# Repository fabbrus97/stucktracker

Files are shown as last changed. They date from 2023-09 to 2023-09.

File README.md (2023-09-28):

# StuckTracker

> [!WARNING]  
> **Experimental work**: This is experimental work. The end result does not function as intended. 

---

This repository contains all the source files - and the report - for the Making class project, at Università di Bologna. 

The aim of the project is to build a self-aligning star tracker, using 3D printed and off-the-shelf components. 

Most of the folders have a `README` with additional information. The repository is organized as follows:

- **bom**: contains the bill of material. 
- **cad**: contains the `.stl` files to be printed, and the original cad file. 
- **code**: contains the python source code, and a `systemd` service file. 
- **report**: contains the report of the project.

> [!NOTE]  
> The electronic schematics are inside the report.

---

Special thanks to Arianna, Stefano, Alessandro and Lorenzo who gave me help throughout the project.

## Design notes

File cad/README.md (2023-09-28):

# CAD Files
This folder contains the cad files.

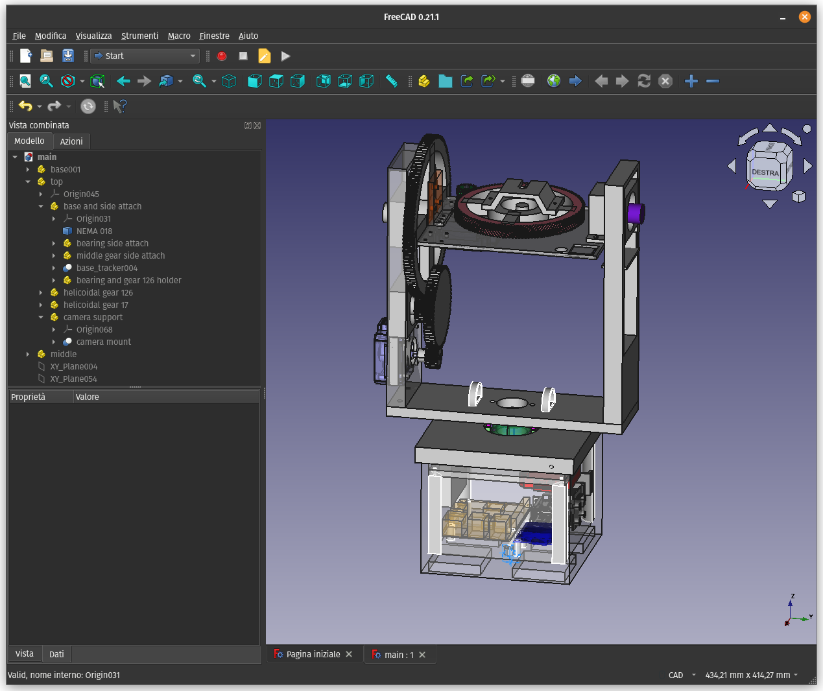
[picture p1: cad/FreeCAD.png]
FreeCAD screenshot.


The files were developed using the FreeCAD software; the main file, containing all the parts, is `main.FCStd`. 

The `std` folder contains all the `.std` files exported from FreeCAD, and organized in subfolders according to their placement and purpose.

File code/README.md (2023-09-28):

# Code
This folder contains the code to run the star tracker. The code was developed for a Raspberry Pi 3B+, and is entirely written in Python.

The required libraries can be installed as root with:
```
# pip3 install -r requirements.txt
```

Furthermore, `startracker.service` can be installed with:
```
# mv startracker.service /etc/systemd/system/
# enable startracker.service
```

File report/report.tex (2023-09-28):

\documentclass[]{article}

\usepackage{pgfplots} 
\usepackage{graphicx}
\usepackage{subfigure}
\usepackage{floatflt}
\usepackage{float}
\usepackage{hyperref}
\usepackage{mathtools}
\usepackage{tikz}
\usepackage{pgf}
\usepackage{cleveref}
\usepackage{xcolor}
\usetikzlibrary{calc,patterns,angles,quotes}
\usepackage{makecell}
\usepackage{tabularx}
\usepackage{listings}
\usepackage{svg}
\usepackage{tablefootnote}
\usepackage[most]{tcolorbox}

\newcommand{\inctrimpic}[2][1]
{}

\include{LaTeX.Listings}
\lstset{style=colorEX}

%opening
\title{Semi-Automatic Portable Star Tracker}
\author{Simone Fabbri \\ simone.fabbri8@studio.unibo.it}

\begin{document}

\maketitle

\begin{figure}[h]
	\centering
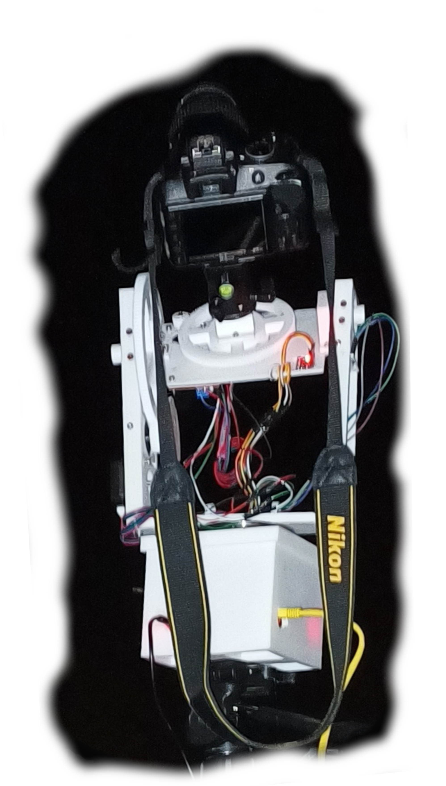
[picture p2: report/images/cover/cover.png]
	
\end{figure}

\begin{abstract}
This is the report of the project developed for the making class at the Computer Science course, university of Bologna.
\\
The scope of this project is to make a portable star tracker, with auto-alignement capability. Star trackers are very useful to photograph stars at night, since longer exposures are required. 
\\
In the following sections will be discussed the main motivations behind this project, the technical details and the conclusion of the report.

\end{abstract}

\begin{tcolorbox}[colback=red!5!white,colframe=red!75!black]
	\textbf{Warning} this is \textit{experimental} work. While the procedure is accurately documented and replicable, the end result is not working, i.e. it does not produce the expected results according to the design goals. The "Results" section shows what can be accomplished in terms of obtainable images. A list of errors and problems can be found in the "Conclusion" section. 
\end{tcolorbox}

\section{Introduction}

\begin{floatingfigure}[r]{0.30\linewidth}
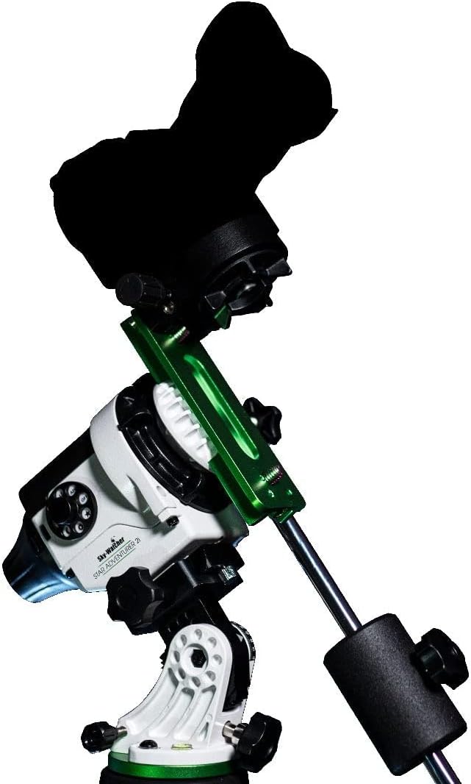
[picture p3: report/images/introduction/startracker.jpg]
	
	\caption{A commercial 500\$ star tracker, the \textit{Skywatcher Star Adventurer 2i.\\}}
\end{floatingfigure}

Capture images of stars is not a trivial task: since they don't emit a lot of light, cameras have a harder time capturing it. 

The only way to capture in a somewhat recognizable way a scarce source of light, is to use a longer time exposure: keeping the camera sensor open for longer time, allows more light to pass. 

But this can only work well for still objects: while stars technically do not move, the earth does, thus the stars seem to move during the night. If a sensor is left open for too much time, a so called "star trail" will start to appear, because the stars will have moved since the start of the capture and their traces will be left on the camera sensor.

To contrast this effect, two solution were developed in the field of photography: 

\begin{itemize}
	\item photo stacking
	\item star tracking
\end{itemize}

The first solution, \textbf{photo stacking}, consists of taking multiple shorter pictures where the stars appear still, i.e. without trails and, using specialized software, "merge" them together. This allows to reduce the noise\footnote{There are different source of noise for a digital image, but the main one in this context is shot noise\cite{shotnoise}: objects emit photons in a random way, and although this is difficult to perceive for humans, it is more evidently in long exposure, dark scene photos, so much that becomes apparent in the photos. } 
in the image, and obtain better quality images.

The second solution is to simply move the camera according to the movement of the stars, using a tool called \textbf{star tracker}: in this way, we can keep the sensor for as long as we want, and the effect of the movement will not be in the image, except for objects in the foreground (e.g. trees, mountains, houses...).

The next sections present the desired features for an optimal solution, the existing solutions for star tracking, and the process of develop a new star tracking system.

\subsection{Requirements for the optimal system}

There are 3 main design goals:
\begin{enumerate}
	\item The star tracker can be used with any commercial DSLR camera and lens.
	\item The star tracker is portable.
	\item The star tracker can be used with any commercial tripod.
\end{enumerate}

These requirements offer the same capabilities of any major commercial solution, thus they define the best solution a \textit{maker} can hope to achieve (given that the total cost is less of a commercial solution) to replicate the same capabilities. In reality, due to limitation of experience, resources, available technologies... the first requirement is relaxed and substituted with the following one:
\begin{enumerate}
	\item The star tracker can be used with any \textbf{small} commercial DSLR camera, \textbf{where "small" means that camera body plus lens should be at maximum about 1 kg.}
\end{enumerate}

Furthermore we want to add another capability:

\begin{enumerate}
	\setcounter{enumi}{3}
	\item The star tracker can auto-align itself, with little to no need for the user to interact with it.
\end{enumerate}

The problem of alignment will be discussed later.

\subsection{Related work}
In this section the focus is on "DIY" or open source solutions, not on commercial ones.

To the best of my knowledge, there are two main projects for DIY star trackers, none of witch fully satisfies the requirement.

\subsubsection{The Micro Scope}

This is a fully functional star tracker \cite{microscope} (technically is a GOTO telescope, but has also tracking capabilities). It can be mounted on a tripod, so it is very portable. The problem is that it not a DSLR star tracker, but there is an embedded camera, so the user cannot attach it's own camera. 

\begin{figure}[H]
	\centering
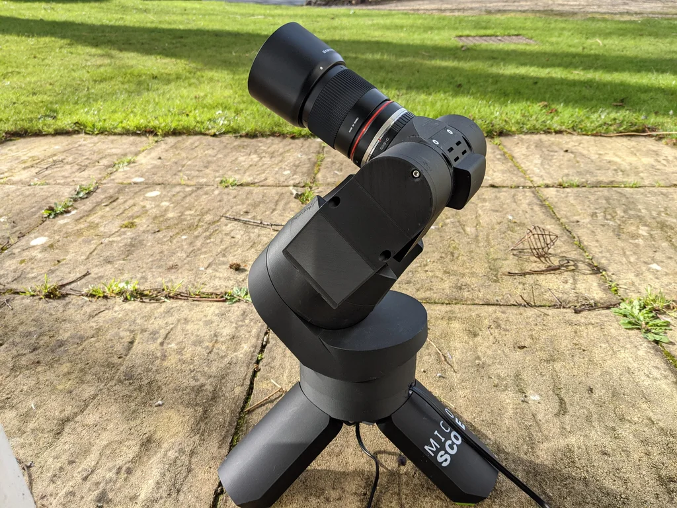
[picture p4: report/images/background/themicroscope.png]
	
	\caption{The Micro Scope DIY goto telescope and tracker.}
\end{figure}

\subsubsection{OpenAstroTracker}

This design was proposed by the reddit user Intercipere \cite{openastrotracker}. This is a very compelling project and probably the best DIY star tracker (and it also has GOTO capabilities), but it has its own standing platform and is considerably bigger than commercial solutions. 

\begin{figure}[H]
	\centering
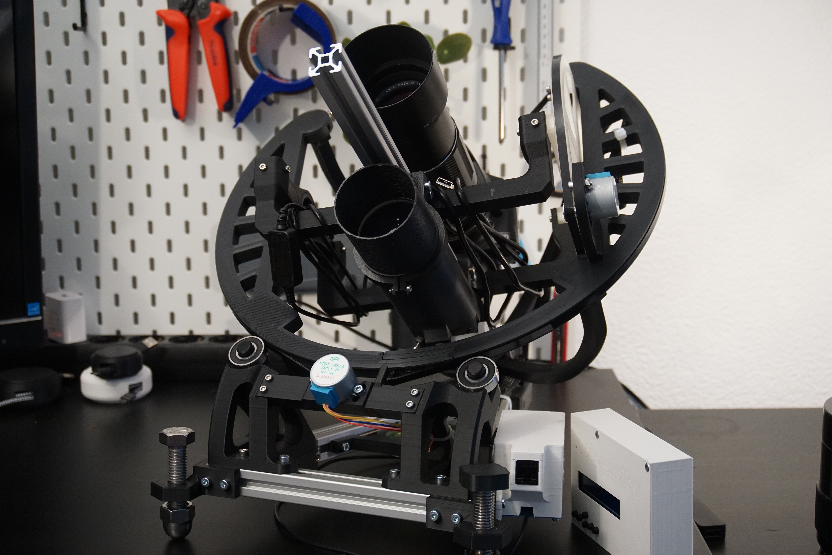
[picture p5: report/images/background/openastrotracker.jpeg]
	
	\caption{OpenAstroTracker, another DIY star tracker.}
\end{figure}

\subsubsection{The OG star tracker}
The \textbf{OG star tracker} \cite{ogstartracker} started and acquired popularity after this project started, so it could not have been considered. This star tracker is a very low-cost solution, can be used with heavy DLSR cameras (up to $3kg$ of payload, and focal length of $300mm$) and is extremely portable. In fact, it fully satisfies the 3 main design goals. What it lacks at the moment is the capability of auto-alignment. 

\begin{figure}[H]
	\centering
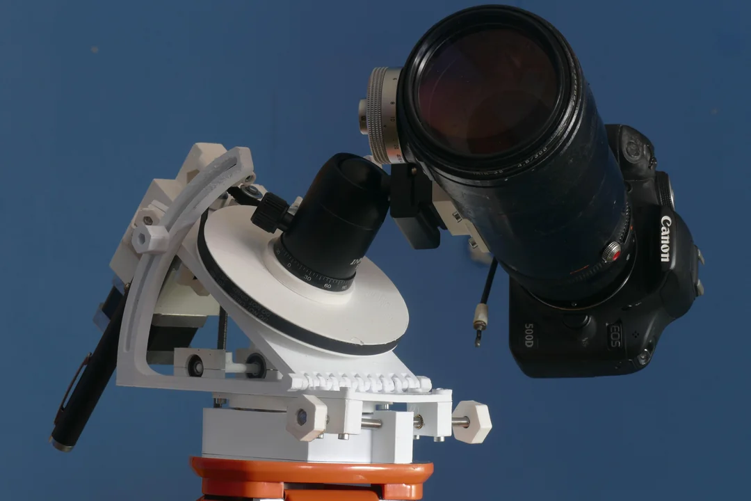
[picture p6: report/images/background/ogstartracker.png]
	
	\caption{The OG Star Tracker, as originally announced on Reddit in the second half of January, 2023 \cite{ogstartrackerreddit}.}
\end{figure}

Since this solution is the most close to the original scope of the project, but it works as intended - unlike my solution, this section will explore more in depth the differences between the two works. 

There are two main differences, which influence the result the most: my experimental solution is based solely on 3D printed gears, which present accuracy problems, while on the OG star tracker only one printed gear was used, and the others are made of metal; furthermore, that projects employs a \textit{gear box}, which can increase very efficiently the output torque utilizing less space, and \textit{drive belts}. 

The second main difference is in the \textit{alignment process}: being completely manual in the OG star tracker, the precision depends only on the human operator; while in this project, it depends on the accuracy and the calibration of the sensors used. This will affect the final results. 

\newpage

\section{Background}\label{sec:intro}

\begin{floatingfigure}[p]{0.35\linewidth}
	\centering
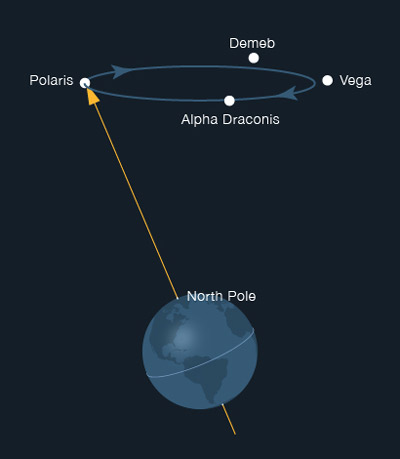
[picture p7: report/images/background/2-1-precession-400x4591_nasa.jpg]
	
	\caption{Polaris is near the Earth's rotation \\}
	\label{fig:polarisnasa}
\end{floatingfigure}	

Before illustrating the details of the developed solution, some technical details about the star tracking process must be understand, in particular why is important to \textbf{align} a star tracker in a certain way. 
\\
\\
The Earth rotates on its axis, with a slight inclination (about 23 degrees) respect to the plane of its revolution around the Sun (its orbit).

Due to this inclination, \textbf{Polaris}, a star also know as the North Star or Pole Star, does not show any movement to the naked eye, since it is very close to Earth's inclination axis. This only works for the northern hemisphere, since Polaris is only visible in this hemisphere. Since Polaris is really bright (relatively speaking), it was also fundamental for navigation. 

All the other stars, on the other hand, that do not lay on the axis, have an apparent movement from east to west. When a camera captures the light from the stars for too long, this movement appears visible \ref{fig:startrail1}. 

While a day on Earth lasts 24 hours, where "day" is defined as the time it takes for the Sun to be visible in the same spot in the sky after the Earth has completed the rotation around his axis, when considering constellation and stars another notion of time should be considered: \textbf{Sidereal Time} \cite{cosmos}. It is the time needed for the "fixed" stars (very distant stars) to appear in the same place on two consecutive nights. This time is shorter than 24 hours by about 4 minutes: 23 hours, 56 minutes and 4.091 seconds. A star tracker needs to perform a complete rotation in the span of sidereal day, not of the 24 hours day. 

\begin{figure}[H]
	\centering
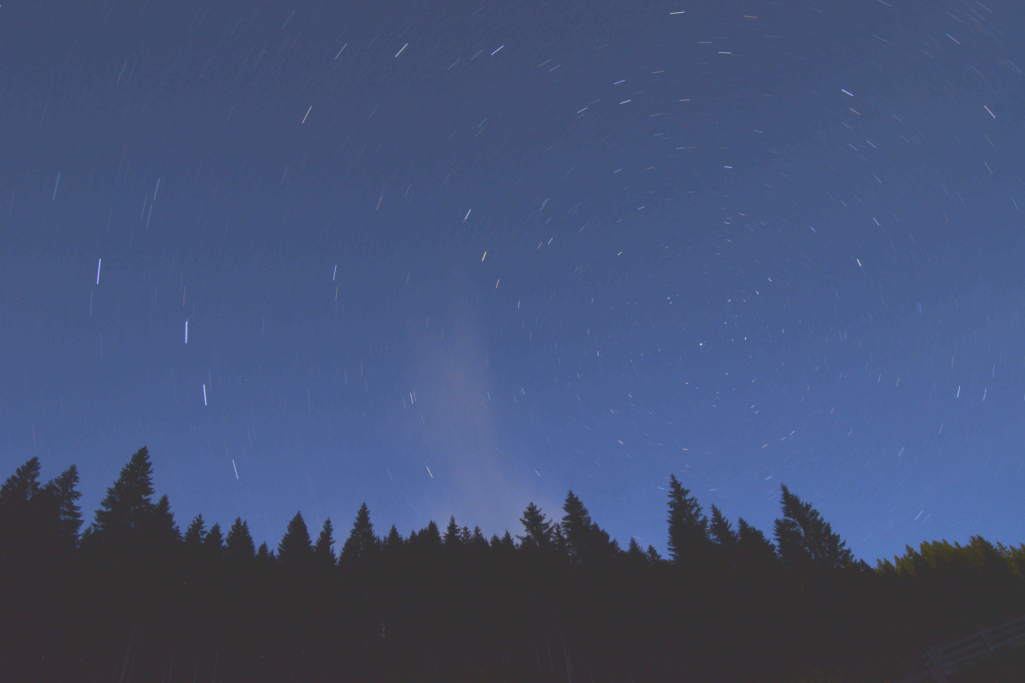
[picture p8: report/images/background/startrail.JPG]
	
	\caption{Star trail visible after about 10 minutes of exposure (Polaris is also visible on the right)}
	\label{fig:startrail1}
\end{figure}

\vspace{1em}

\subsection{Camera basics and the 500 rule}
How fast the "star movement" starts to become evident, depends on the lens and the camera specifications. 

The first important factor is called \textbf{focal length}, and, to simplify, is the level of zoom the lens has. So, the bigger the focal lens, the lesser the angle of view will be; and of course also the magnification will be bigger. 

\begin{figure}[H]
	\centering
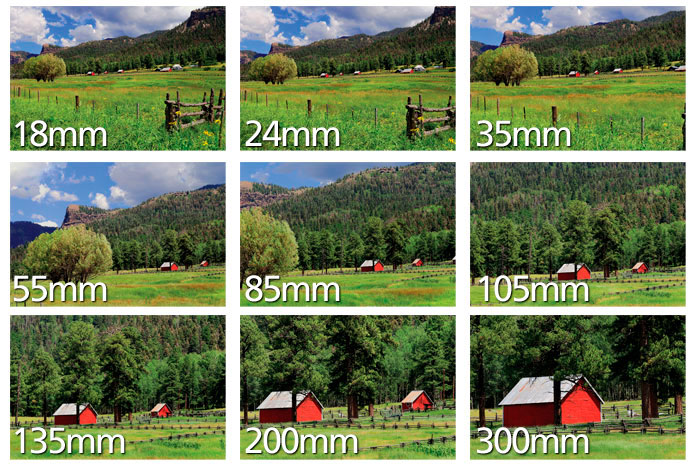
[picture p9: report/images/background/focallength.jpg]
	
	\caption{Lens focal length tells us the angle of view - how much of the scene will be captured - and the magnification - how large individual elements will be \cite{nikon}. Notice the difference between 18mm and 300mm.\\}
\end{figure}

When a moving object is magnified, its movement will be "amplified"; this implies that with a greater focal length, the \textit{star trail} effect will appear with less exposure time; on the other hand, with less magnification the object will appear still for longer time. 

Another important element is the \textbf{crop factor}. Before digital, a common film size was 35mm, meaning that an image going through a lens was impressed on a light-sensible film, with a rectangular shape of a certain size (35mm was the size of the film, side to side).

\begin{figure}[H]
	\centering
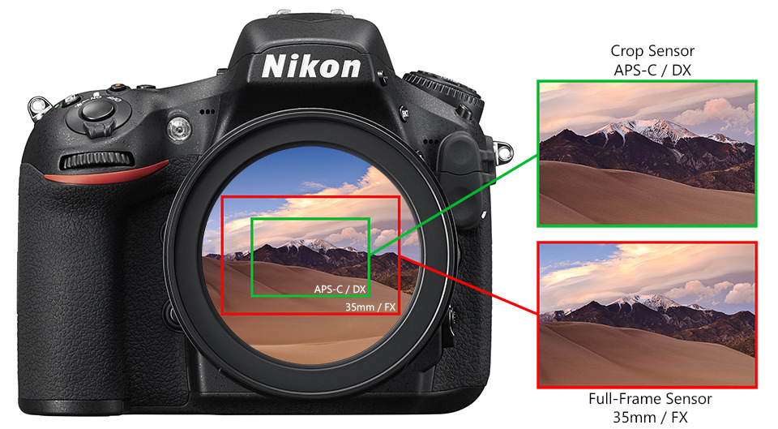
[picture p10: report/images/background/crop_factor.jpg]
	
	\caption{Crop factor visualization \cite{cropfactor}: a Full-Frame vs APS-C Sensor size are compared.\\}
\end{figure}

With digital, sensor sizes changed, and the same image passing though the lens now can hit a different amount of space, depending on the size of the underlying sensor, so the final image is "cropped" respect to a 35mm film. 

There are different common standard sizes for digital camera sensors, but we will refer to the APS-C size, wich has a crop factor of 1.5. The crop factor is the ratio of sensor size to the 35mm, and helps lens manufacturer and photographers understand what the final field of view of the camera will be. 

After having introduced these two concepts, focal length and crop factor, it is possible to introduce the \textbf{500 rule}  \cite{500rule}. This is an empirical rule to compute the maximum exposure time usable before the star trail effect appears. 

The rule can be expressed as:

$$ SS = \frac{500}{CF \cdot FL}$$

where $SS$ is the exposure time, or \textit{shutter speed}, $CF$ is the crop factor and $FL$ is the focal length. The graph \ref{pic:500graph} shows the shutter speed for different focal lengths, and a crop factor of 1.5:
\\
\\
\begin{figure}[H]
	\centering
	\begin{tikzpicture}
		\begin{axis}[
			width=\textwidth,
	  		title={Exposure time before star trail appears (crop factor = 1.5)},
			xlabel={Focal length in mm},
			ylabel={Shutter speed in seconds},
			xtick={18, 28, 38, 48, 58, 68, 78, 88, 98},
			]
			\addplot [ 
			domain=18:98, 
			color=red,
			mark=square, 
			samples = 9,
			nodes near coords, 
			xtick={18, 28, 38, 48, 58, 68, 78, 88, 98},
			]
			{500/(1.5*x)};
		\end{axis}
	\end{tikzpicture}
	\caption{This graph shows the shutter speed computed through the 500 rule. Increasing the focal length (from 18mm to more than 90), the exposure time for a shot without trail decreases.}
	\label{pic:500graph}
\end{figure}

\iffalse
\subsubsection{Right Ascension and Declination}
Since Polaris is not exactly on the Earth's rotation axis, other important concepts are right ascension and declination.  

Every point on Earth can be localized through two coordinates, \textbf{latitude} and \textbf{longitude}, which are respectively the distance in degrees north or south of the equator, and the distance in degrees east or west of the prime meridian\footnote{The prime meridian is the imaginary line connecting the poles and passing through Greenwich.}. 

\begin{figure}[H]
	\centering
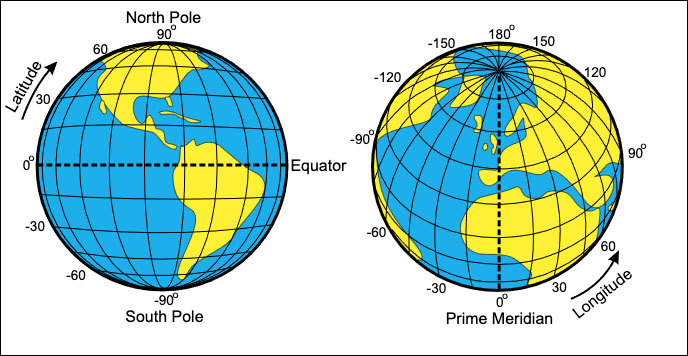
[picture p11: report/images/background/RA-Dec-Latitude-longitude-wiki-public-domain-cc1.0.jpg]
	
	\caption{Earth is shown covered in an imaginary grid of latitude lines (measured from $0^{\circ}$ to $90^{\circ}$ north and south of the equator) and longitudes lines (measured from $0^{\circ}$ to $180^{\circ}$ east and west of the prime meridian).}
	\label{fig:latlon}
\end{figure}

Right ascension and declination are the coordinates of celestial objects: declination corresponds to latitude, and right ascension to longitude. To accurately find a celestial object, like Polaris, is very useful to know these coordinates. 

\begin{figure}[H]
	\centering
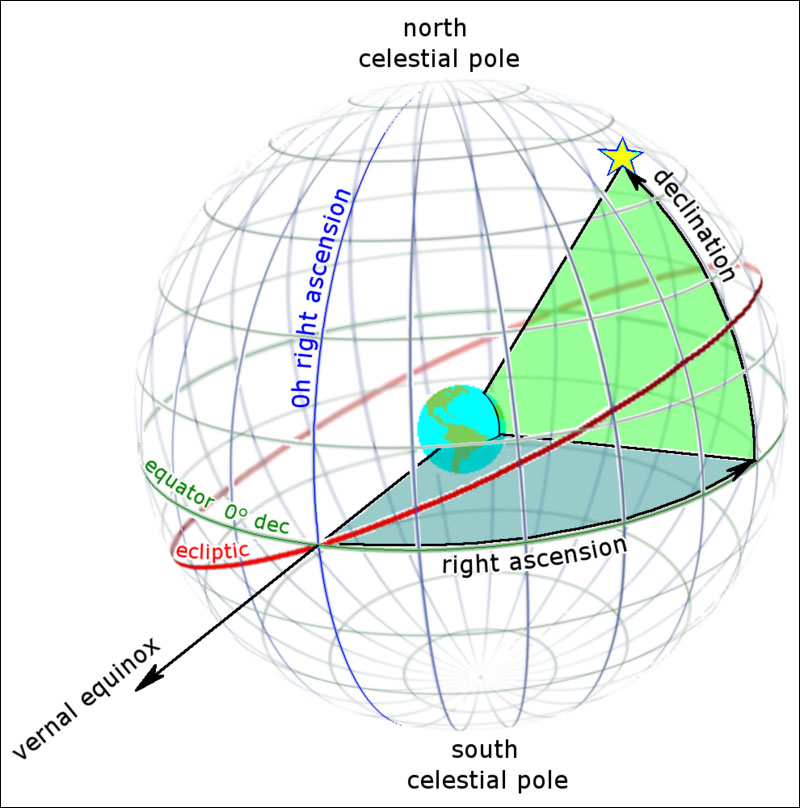
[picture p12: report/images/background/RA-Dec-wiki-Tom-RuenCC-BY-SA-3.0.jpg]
	
	\caption{Declination (green) is measured in degrees north and south of the celestial equator. Right ascension, akin to longitude, is measured east from the equinox. The red circle is the Sun's apparent path around the sky, which defines the ecliptic.}
	\label{fig:radec}
\end{figure}

Earth's equator, at $ 0^{\circ} $ latitude, becomes also the
 \textit{celestial equator};   declination is measured in degrees: e.g. Polaris has a declination of $ +89^{\circ}  15^{\prime} $. 

The right ascension is slightly more complicated. The $0^{\circ}$ mark in the sky separating the east form the west is placed at the \textbf{vernal equinox}. This is the spot where the sun arrives on the first day of spring. But right ascension is measured in hours: the sky can be treated as a clock, since it wheels by as Earth rotates. And ascension is also measured in one direction, east. There are 24 lines for the right ascension hours, as a day on the Earth lasts 24 hours. Polaris has a right ascension of $2^h 41^m$.

\begin{figure}[h!]
	\centering
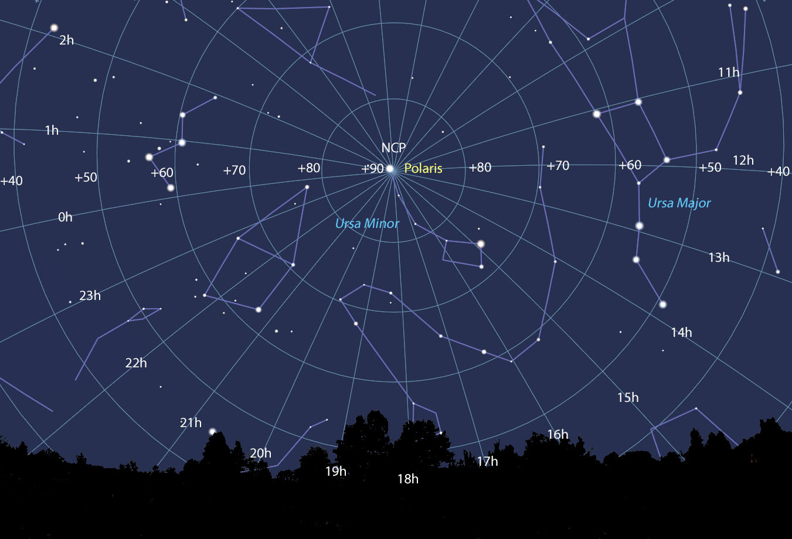
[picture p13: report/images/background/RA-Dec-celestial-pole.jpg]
	
	\caption{This view shows the north celestial pole (NCP) and polar regions. Declinations are labeled every 10° and the hours of right ascension are shown around the circle. By convention, 0h is used instead of 24h. 
		\textit{Stellarium}}
	\label{fig:stellarium}
\end{figure}
\fi 

\subsection{Magnetic declination} \label{sec:mag_decl}
\begin{floatingfigure}[r]{0.4\linewidth}
	\centering
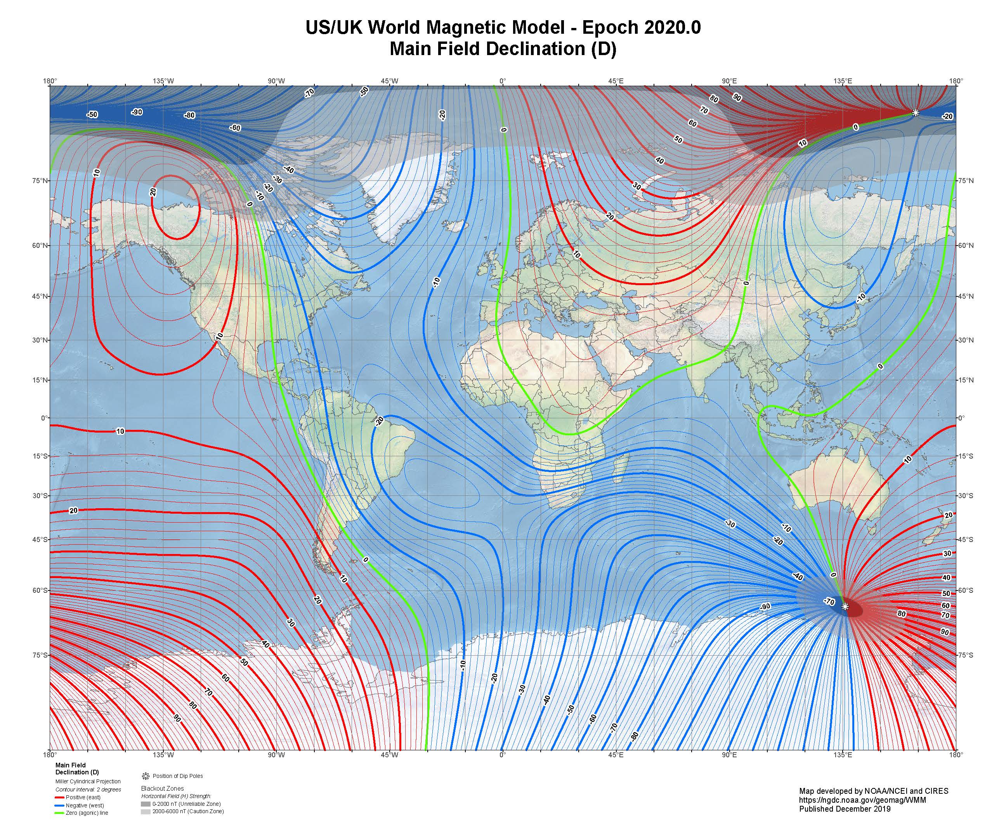
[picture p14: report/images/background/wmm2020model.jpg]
	
	\caption{The WMM2020 declination projection \cite{wmm2020}. The declination is considered positive when the angle measured is \textcolor{red}{east} (red lines) of true north and negative when \textcolor{blue}{west} (blue lines).\\}
\end{floatingfigure}

The Earth has a magnetic field; but this is not uniform across the globe. It even changes with time \cite{magndecl}

Hence, compasses can only point towards the \textbf{magnetic north}, which can vary from place to place, and not to the \textbf{geographic north}. 

The magnetic field - and the magnetic north - forms an angle with the geographic north; this angle is called \textbf{magnetic declination}. 

It is possible to compute in advance and know how much this angle is, given the position and the time. \textbf{The World Magnetic Model} \cite{wmm2020} is the standard model used in navigation to account for the magnetic declination. This model is produced at 5-year intervals, with the current model expiring on December 31, 2024.
\\
\subsection{Polar alignment}
Now it is possible to put together all the concepts previously presented. 

The idea behind star tracking is to move the camera according to the rotation of the Earth, in order to compensate for this movement. To achieve this, a star tracker needs to rotate very slowly  - a complete rotation has to happen in a sidereal day time   - in the same way and speed as the stars seem to move, from east to west. Furthermore, a star tracker needs to be aligned with the axis of the movement, which is the rotational axis of the Earth. 

This is accomplished trough \textbf{polar alignment}: the star tracker needs to be aligned with the Earth's rotational axis, which is achieved when the star tracker points to Polaris \cite{polaralignment}. If great precision is required, e.g. when we want to use a big focal length, then an exactly alignment is absolutely necessary; but when there is no such requirement, pointing towards Polaris should be sufficient.

\begin{figure}[H]
	\centering
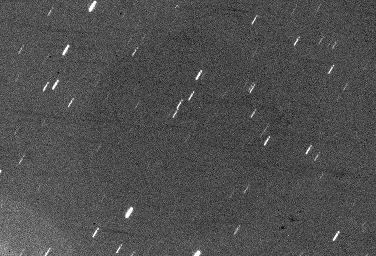
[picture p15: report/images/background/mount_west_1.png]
	\subfigure[Polar drift]{}
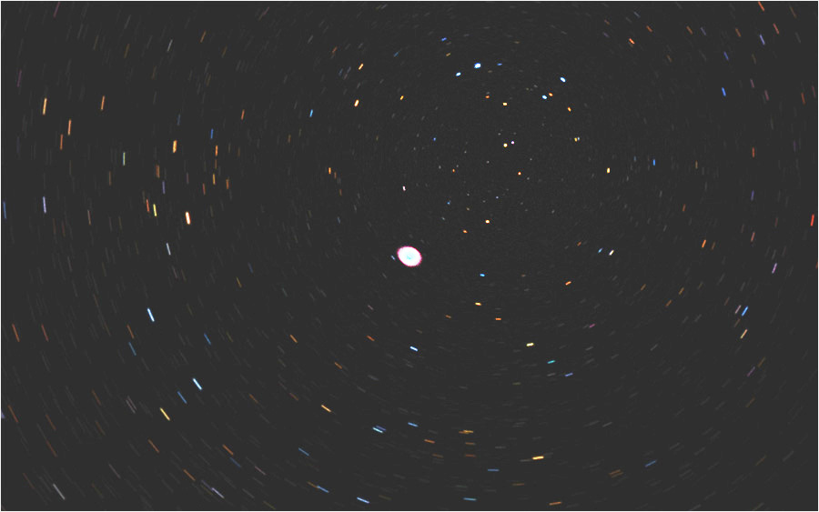
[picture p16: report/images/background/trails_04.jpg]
	\subfigure[Field rotation]{}
	\caption{Examples of misalignment. The first is a case of general \textit{polar drift} \cite{drift}: the mount was adjusted a small amount west and above the pole; the second is a case of \textit{field rotation} \cite{fieldrotation}: the stars seems to rotate around the guide star in the field.\\}
	
\end{figure}

While it is possible to exactly point Polaris with a special scope, called the \textit{polar scope}, its position can be determined by knowing the observer's latitude and where the geographic north is: in fact, as previously discussed, Polaris is above Earth's rotation axis, which passes through the poles, so Polaris is above the North Pole. The latitude is useful to know how many degrees to look up above the horizon to find the star: for example, an observer located at $ +44^{\circ}  15^{\prime} $ should point towards north and look up around $ 44^{\circ}$ from the ground. 
\\
\\
Finally, there is a type of mounting mechanism that allow to rotate a telescope or camera to track the movement of the stars: an \textbf{equatorial mount}. These are designed more specifically for astrophotography, since allow for longer exposure time. There is another type of mount to observe the sky with a telescope or a camera, an \textbf{alt-azimuth} mount: this is a slightly simpler mechanism, but it doesn't allow for long exposure time, so it is not suitable for astrophotography. 

As previously discussed, an equatorial mount needs to be aligned with Polaris in the most precise way possible; the camera is then mounted on top and it rotates as required. 

\section{Design of the star tracker}
After discussing what the requirements for the project are, and some background in astrophotography, the following sections provide implementation details. 

This section is about the case for the various components, such as sensor, motors and battery. 

All the case components were developed using a cad software, \textbf{FreeCAD} and printed using a 3D printer, the \textbf{Creality Ender 3 Pro}. The material used is \textbf{PLA}. 
 
While the use of this technique introduces stability and precision problems, it is really cheap and quick to build simple prototypes. This affects in some ways  the final result, but for an "experiment" such as this one is more than suitable. 

There are also some minor errors such as wrong holes dimension, that were not corrected because it required reprinting entire parts; since these errors do not compromise the final build, were corrected with traditional tools (such as sandpaper), require a waste of time and material to reprint the corrected part and in general are not relevant to the design of the star tracker, they are omitted in the rest of the report. 
\\
\\
The star tracker is an \textbf{equatorial mount}, has a hole at the bottom to be mounted on a tripod and is composed of three parts, which will be referred as \textit{base}, \textit{middle} and \textit{top}. 

Details about the electric and electronic components will be omitted in this section, to be discussed thoroughly in the next section.  

\subsection{Base}
The base of the star tracker is a cube and it fits:
\begin{itemize}
	\item a \textbf{Raspberry Pi 3B+}: performs all the computation;
	\item the \textbf{input system}: button, led and a switch
	\item a \textbf{battery}: it powers all the motors
	\item a \textbf{gps} sensor and its \textbf{antenna}
	\item two \textbf{DC-DC} converters
	\item a \textbf{battery charger circuit}
	\item two \textbf{motor drivers}
	\item a \textbf{stepper motor}
	\item a \textbf{intermediate section} composed of: 
	\subitem{-} a \textbf{flat surface}, to separate all the previous components 
	\subitem{-} two \textbf{gears} that rest on the surface, to rotate the \textit{middle} part
	\item a \textbf{lid}, to close the cube
\end{itemize}

On the bottom of this cube there is a \textit{1/4 inch threaded hole}, which is the standard format for photographic screws: this allows the base to be mounted on any standard tripod. The base was also printed with some "missing" parts on the bottom, to reduce the material required for the print; in the inner side of the bottom, there are some empty cylinders to screw some of the components; other holes are on the side of the cube, and the relative components are keep in place vertically.

\begin{figure}[H]
	\centering
	\subfigure[Bottom]
		{}
	\subfigure[Side]
		{}
	
	\caption[Bottom of the base]{(a) is the bottom of the base; it is visible the hole for the photographic screw. In (b), on the side, the holes are for led, buttons, a switch and a recharge circuit. }
	\label{fig:basecolumns}
\end{figure}

In the inner of the cube there are four "columns", on the vertexes: it allows the flat surface to be screwed inside the cube, on the top of these columns. 

\begin{figure}[H]
	\centering
	
	\caption[Bottom of the base]{The green elements are the columns where the flat surface is screwed. There are also visible the little cylinders to screw the components such as the Raspberry.}
	\label{fig:basebottom}
\end{figure}

On the side, there are the holes for the user input (and output) system: the four little squares were intended for two led and two buttons, although only one for each is used,  the big rectangle is for the switch and the lower one is for the recharge circuit. 

On the flat surface, at its centre, there is an \textbf{empty cylinder}: this allows all the cables to pass through the centre of rotation of the middle part, and reduces the possibility of \textbf{twisting} the cables rotating the middle. 

\begin{figure}[H]
	\subfigure[flat surface]
		{}
	\subfigure[base gear]
		{}
	\caption{In (a) is visible the flat surface that lies on top of the four columns, and in (b)the gear that rotates the \textit{middle} part.}
\end{figure}

The intermediate flat surface has also some holes to allow a motor to be mounted below it: on the motor, there is a \textbf{gear} that makes a bigger gear on the previously introduced cylinder to rotate; this in turns rotates the middle part. 
The bigger gear is also inserted on a bearing ball.

The lid simply keeps the bigger gear in place, and another bearing ball
where the middle part rests. It is screwed to the base with two screws on the side.

Another two holes were manually added on the side to allow the raspberry to be powered through the USB port, and to be connected with its Ethernet port. 

\subsection{Middle}

This part was not printed as one piece, but as three separate pieces: the bottom one and the two sides. The sides are screwed to the bottom part, to form a \textit{u} shape. 

\begin{figure}[H]
	\centering
	\inctrimpic[0.7]{images/design/middle/middle_iso.pdf}
	\caption{This is the \textit{middle} part of the star tracker, in green. The other parts are auxiliary parts mounted on it.}
	\label{fig:middle_iso}
\end{figure}

The middle part allows the system to rotate towards the north. On this part there is:

\begin{itemize}
	\item a \textbf{motor}, that moves \textbf{three gears}
	\item an \textbf{Adafruit} chip with magnetic, gyro and accelerometer sensors
\end{itemize}

The motor is mounted at the bottom, and is connected to three gears, to increase its output torque. This is essential because it can raise the \textit{top} part, according to the latitude read by the gps sensor. 

The two bigger gears have a cylinder in their middle, that is then inserted in bearing ball.

\begin{figure}[H]
	\centering
	\subfigure
		{}
	\subfigure
		{}
	\caption{In this picture, all the other 3D printed parts are visible mounted on the \textit{middle} part. }
	\label{fig:middle_all}
\end{figure}

The bearing ball
is then fixed in another 3D printed rectangle, that is screwed on the sides of the "arms" of the \textit{middle} part. 
\\
\\
The Adafruit magnetometer sensor can be affected by the magnetic field generated by the motors, so it is mounted in the most far position possible on the opposite side of the motor. 

The \textit{top} part is supported thanks to some screws on the bigger gear on one side, and a bearing ball
on the other side. The bearing ball
is supported thanks to a 3D printed rectangle, as discussed before. 
\\
\\
At the bottom, the two small arcs are used to run the cables through them, to minimize the possibility of twisting. 

\subsection{Top}

The \textit{top} part is where the tracking actually occurs; here is mounted:
\begin{itemize}
	\item \textbf{3d printed parts} to attach it to the \textit{middle}
	\item a \textbf{motor} with two \textit{gears} and a \textbf{support} to attach a camera
	\item an \textbf{accelerometer sensor}
	\item a \textbf{motor driver}
	\item a \textbf{support} for a gear
\end{itemize}

This is also the simplest part: the accelerometer is used to determine the plane inclination. The inclination must be the same of the latitude. 

The gears provide the actual tracking: the camera is mounted on top of the biggest gear, that rotates accordingly to the rotation of the Earth, through  a support, that is actually screwed to the gear and connects them. 

\begin{table}[H]
	\centering
	\subfigure[]{\inctrimpic[0.32]{images/design/top/top_empty.pdf}}
	\subfigure[]{\inctrimpic[0.32]{images/design/top/top_sides.pdf}}
	\subfigure[]{\inctrimpic[0.32]{images/design/top/top_gear_support.pdf}}
	
	\subfigure[]{\inctrimpic[0.45]{images/design/top/top_gears.pdf}}
	\subfigure[]{\inctrimpic[0.45]{images/design/top/top_cam_support.pdf}}
	\caption{The \textit{top} part: (a) is empty; in (b), (c) and (d) 3D printed parts are
	 sequentially added. (e) shows the support where the camera can be screwed. }
	\label{tab:topseq}
\end{table}

\section{Motors and gears}

This section provides details about the motors and the gear moved by them. 

\subsection{Motors}
The motors were chosen with two main specifications:

\begin{enumerate}
	\item the motors should be \textbf{lightweight}, and requiring a small amount of \textbf{tension/current}
	\item the motors can be driven \textbf{precisely}
\end{enumerate}

Keeping the motors lightweight and with little electric requirements, allows for a more light overall structure, and to use a smaller battery, thus maintaining the star tracker more portable. 

On the other hand, if the weight that a motor needs to raise/move is too high, a well-crafted and thought \textbf{gear-set} must be used, introducing more complexity and requiring more space to insert it. The gears will be discussed in the next subsection.

As regards the second requirement, the most suitable type of motor to fulfil it is the \textbf{stepper motor}.

A stepper motor is an electromagnetic motor, that can be moved in \textbf{steps}, where each step corresponds to a certain degree of movement. A stepper motor can be driven in a way that each current impulse generates a certain amount of steps. 

For this project, two models of motor were chosen: a \textbf{Nema 17HS15}, to rotate the \textit{middle} part and incline the \textit{top} part, and a \textbf{Nema 17HS4023} for the tracking movement. These motors have the desired requirements, and are driven with two circuits that will be discussed in the next session. 

The motors' specification are summarized in table \ref{table:motor}.
\\
\\
The motor in the \textit{base} does not actually rotate the \textit{middle} part, but it \textbf{"vibrates"} (rotating very fast clockwise and anticlockwise) to tell the user how to rotate the part by hand; this solution was adopted because the 3D printed parts do not allow a precise installation and movement of them, and there is \textbf{too much friction} in some teeth of the gears to allow the motor to rotate them smoothly; so a "manually" approach was chosen, with the motor simply used to act as an indication for the user, who performs the action in place of the motor. 

Other than movement/vibration, the motors perform another important function: they lock the gears in place, to stop them from moving after being placed in the right position.

\begin{table}
	\centering
	\begin{tabular}{|c|c|c|c|c|}
		\hline
		Name & Stepping Angle & Current & Tension & Torque \\
		\hline
		\textbf{Nema 17HS15} & $1.8^\circ$ & $1.5A$ & $12V$ & $45N\cdot cm$ \\
		\hline
		\textbf{Nema 174023} & $1.8^\circ$ & $1A$ & $4V$ & $13N\cdot cm$ \\
		\hline
	\end{tabular}
	\caption{Motors' specifications.}
	\label{table:motor}
\end{table}

\begin{figure}[h]
	\centering
	\inctrimpic[0.7]{images/motors/motors_placement}
	\caption{Motors' placement: the purple one is a different model than the red ones.}
	\label{fig:motorplacement}
\end{figure}

\subsection{Gears}
In this subsection, the design of the gears is discussed; after introducing the gears individually, they are presented as gear-sets. The table \ref{tab:gears}
summarizes all the gears used. 
\begin{table}
	\centering
	\begin{tabular}{|c|c|c|c|}
		\hline
		N. of teeth & Module & Positions & N. of gears \\
		\hline
		17 & 0.8 mm & \textit{base, top\tablefootnote{The gear in the top is a helicoidal gear, although with the same specifications.}} & 2 \\
		\hline
		64 & 0.8 mm & \textit{base} & 1 \\
		\hline
		17 & 1 mm & \textit{middle} & 1 \\
		\hline
		24, 64\tablefootnote{
		This gear is composed of two gears printed one on the other. 
		} & 1 mm & \textit{middle} & 1 \\
		\hline
		127 & 1 mm & \textit{middle} & 1 \\
		\hline
		126 & 0.8 mm & \textit{top} & 1 \\
		\hline
	\end{tabular}
	\caption{Table representing all the gears used; the last column refers to the number of printed gears.}
	\label{tab:gears}
\end{table}

The gears were designed with the CAD software \textit{Freecad}, using the \textit{part design} mode. 

A gear can be simply created specifying the \textbf{number of teeth} and the \textbf{module}, which is the number of millimeters of pitch diameter divided by the number of teeth and is used to describe the size of the teeth.

\subsubsection{Base gears}

There are only two gears: one, which is screwed to the motor, and the other, which is connected to the first and provides the rotation to the \textit{middle} part.

The first gear has 17 teeth, the second 64. The first gear has a "hole" on its side, so a nut can be inserted to screw in a bolt which pressed against the motor shaft to keep it in place.

The 64 teeth gear has an empty space at its bottom to contain a bearing ball.

\begin{figure}[h]
	\centering
	\subfigure{\inctrimpic[0.45]{images/motors/mot_17_mod08.pdf}}
	\subfigure{\inctrimpic[0.45]{images/motors/mot_17_mod08_2.pdf}}
	\caption{The 17 teeth gear in the \textit{base}.}
	\label{fig:17base}
\end{figure}

\begin{figure}[h]
	\centering
	\subfigure{\inctrimpic[0.45]{images/motors/mot_64_mod08.pdf}}
	\subfigure{\inctrimpic[0.45]{images/motors/mot_64_mod08_2.pdf}}
	\caption{The 64 teeth gear in the \textit{base}. In the second image, the space for the bearing ball is visible.}
	\label{fig:64base}
\end{figure}

It is now possible to consider the gears as a \textbf{gear-set} and compute the \textbf{output torque}. 

The formula to compute it, which will be also used in the next subsections, is the following:

$$ \textnormal{output torque} = \frac{\textnormal{teeth of driven}}{\textnormal{teeth of driver}}\cdot \textnormal{input torque}$$
\\
\\
The motor used in the \textit{base} produces around \textbf{17} $N\cdot cm$ of \textbf{torque}. Since this output is applied to a 17 teeth gear, which is connected to a 64 teeth, this gives an output of around $ \frac{64}{17}\cdot{17} = 64 N\cdot cm$.

In the actual setup, the motor is rated for 1 Ampere of current, the driver nominal continuous current is $0.8A$, with peaks above $1A$; since the torque depends is proportional on the current \cite{steppermcurrent}, the output torque should be lower. 

In fact, this motor is used as a "vibrator", and not to move the upper parts, as will be described in section \ref{sec:software}, in the paragraph dedicated to the gps and north alignment. The user itself rotates the \textit{middle} part, using the indications provided by the motor's vibration.

\subsubsection{Middle gears}

In the \textit{middle} part, there are 4 gears, although 2 of them are printed together. 

The smallest one, is identical to the one in figure \ref{fig:17base}, except for the module, which is slightly larger. 

In this setup, there are more gears connected, but the formula to compute the output torque is the same. The second gear consists of a 24 teeth and a 64 teeth gears, and has a cylinder to be put inside a bearing ball, and facilitate its rotation. Its function is to connect the 17 teeth to the 127 teeth gear, which is also connected to a bearing ball.

\begin{figure}[h]
	\centering
	\subfigure[]{\inctrimpic[0.45]{images/motors/mot_middle_64_24.pdf}}
	\subfigure[]{\inctrimpic[0.45]{images/motors/mot_middle_127.pdf}
	}		
	
	\subfigure[]{\inctrimpic[0.7]{images/motors/mot_middle.pdf}}
	\caption{(a) is the 24/64 teeth gear, (b) is the 127 teeth gear and (c) are all the gears connected with the motor.}
	\label{fig:middle_gears}
\end{figure}

The purpose of the 127 teeth gear is to rotate the \textit{top} part.

These gears are connected to another $17 N \cdot cm$ motor; so the output torque $OT$ is given from:

\begin{align*}
	OT & = \frac{64}{17}\cdot \frac{127}{24}\cdot 17 \\
	   & = 3.76 \cdot 5.29 \cdot 17\\
	   & = 338.14 N\cdot cm
\end{align*}
\newpage
\subsubsection{Top gears}

There are two \textit{top} gears, a smaller one connected to the motor, and a bigger one, which rotates the camera and provides the actual tracking (fig. \ref{fig:topgears}). These gears differ from the others because they are double helicoidal, to provide better contact between them. 

These gears have 17 and 126 teeth; they are connected to a more powerful motor than the other gears; the torque of the motor is:

\begin{align*}
	OT & = \frac{126}{17}\cdot 45 \\
	& = 333.53 N\cdot cm
\end{align*}

\begin{figure}[H]
	\centering
%	\subfigure[]{\fbox{\includegraphics[trim=0 200 0 200, clip, width=0.45\linewidth]{images/motors/mot_top_gear_17.pdf}\label{fig:topgears1}}}
	\subfigure[]{\inctrimpic[0.45]{images/motors/mot_top_gear_17.pdf}\label{fig:topgears1}}
	\subfigure[]{
		\inctrimpic[0.45]{images/motors/mot_top_gear_126.pdf}\label{fig:topgears2}
		}
	\subfigure[]{\inctrimpic[0.6]{images/motors/mot_top_gears.pdf}\label{fig:topgears3}}
	\caption{(a) is the small, 17 teeth \textit{top} gear; (b) is the bigger, 126 teeth \textit{top} gear; (c) shows the disposition of the two gears together. In (a) the double helicoidal pattern of the teeth is very noticeable.}
	\label{fig:topgears}
\end{figure}

The camera does not sit directly on top of the 126 teeth gear; there is a support (it is cyan in figure \ref{fig:topgears3}).

The support allows for a camera ball-head to be mount on it, such as the one in figure \ref{fig:camerahead}, with a screw holding them together.

\begin{figure}[h]
	\centering
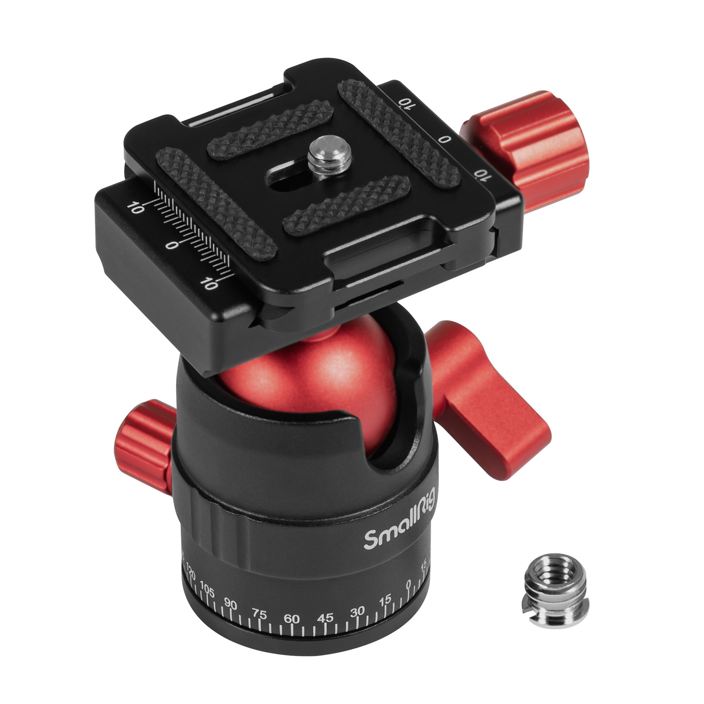
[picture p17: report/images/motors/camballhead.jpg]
	
	\caption{A camera ball-head that can be mounted on the support on the 126 \textit{top} gear.}
	\label{fig:camerahead}

\end{figure}

Since the camera is placed on the \textit{top} plane, which can be tilted by some degree $\alpha$ (figure \ref{fig:moment}) with reference to the ground, it is possible to compute whether the motor can turn the camera for various values of $\alpha$. For simplicity, only rotation in the $xz$ plane will be considered (figure \ref{fig:xzplane}). 

\begin{figure}[H]
	\centering
	\subfigure[]{
		\begin{tikzpicture}
			\pgftext
			[at=\pgfpoint{0cm}{0cm},left,base]
			{
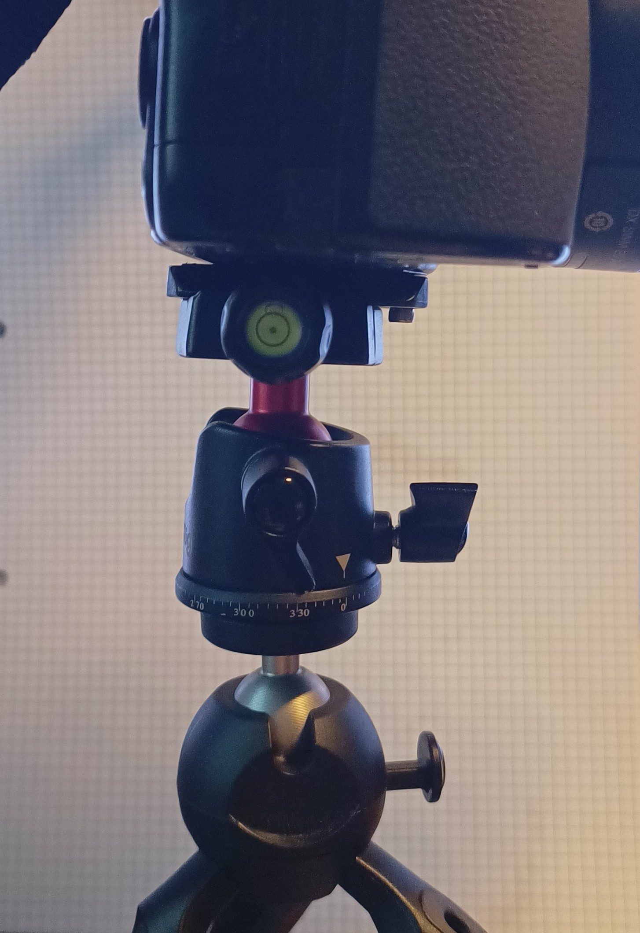
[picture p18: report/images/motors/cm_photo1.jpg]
				
			}
			\node (orig) at (0.5, 1.2) [draw=none] {};
			\draw[line width=1pt, color=white, arrows=->] (orig) -- +(0, 2);
			\draw[line width=1pt, color=white, arrows=->] (orig) -- +(2, 0);
			
			\node (xt) at ($(orig) + (0, 2.1)$) [draw=none, color=white] {z};
			\node (xt) at ($(orig) + (2.1, 0)$) [draw=none, color=white] {x};
		\end{tikzpicture}
		\label{fig:xzplane}
	}
	\subfigure[]{
		\begin{tikzpicture}
			\pgftext
			[at=\pgfpoint{0cm}{0cm},right,base]
			{
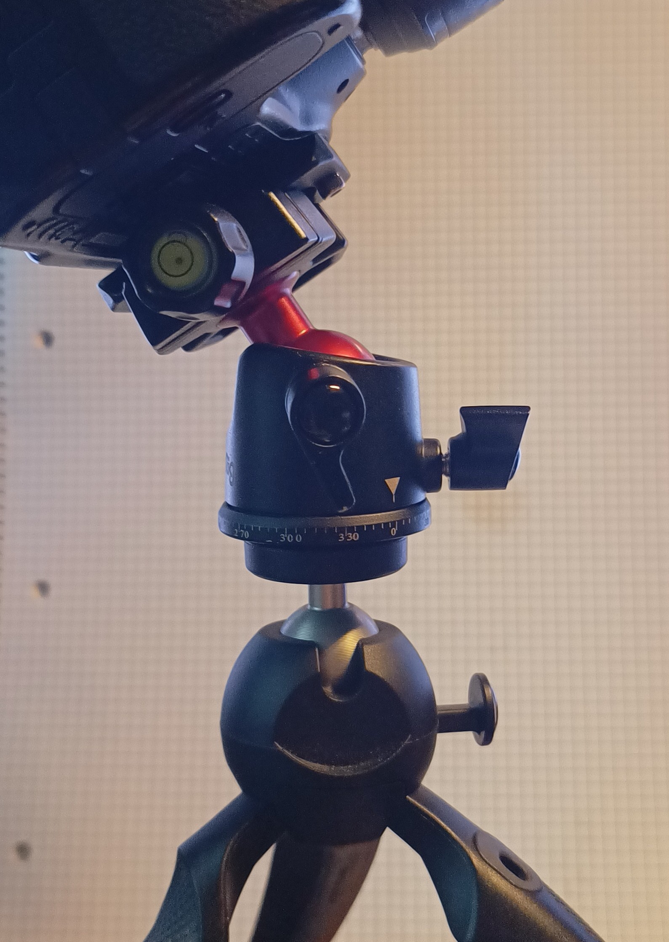
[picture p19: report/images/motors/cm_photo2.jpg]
				
			}	
			\node (base) at (-2, 2) [inner sep=1pt, circle, fill=orange] {};
			\draw [line width=2pt, color=white] 
			(base)+(-1, 0) -- +(1, 0) ;
			\fill[pattern = north east lines, pattern color=white]  ($ (base) + (-1, 0) $)  rectangle  ($ (base) + (1, -.2) $)  ;
			
			\node (G) at ($(base) + (-0.1, 1.4)$) [circle,draw=white,inner sep=1pt,fill=red] {};
			\draw[line width=.6pt, color=black] (G)+(-1, 0) -- +(1, 0) ; 
			\draw[line width=.6pt, color=blue] (G)+(-1.1, -0.1) -- +(.9, 1.3) ; 
			\draw[thick, color=orange] (G)+(.5, 0) arc (0:45:1.1cm);
			
			\node (groundt) at ($(base) + (0, .2)$) [draw=none, scale=0.7, white] {ground};
			\node (betat) at ($(G) + (.3, .3)$) [draw=none, color=orange, scale=.7] {$\beta$};
			\node (betat) at ($(G) + (1, .15)$) [draw=none, color=black, scale=.5] {\textit{top} plane};
		\end{tikzpicture}	
		\label{fig:beta}
	}
	\caption{(a): only rotation in $xz$ plane will be considered; the camera is also parallel to the \textit{top} plane, i.e. the head-ball is not rotated. Note that, in general, the \textit{top} plane can be at various angles $\alpha$ w.r.t the ground. (b): $\beta$ is the angle of the camera w.r.t. the \textit{top} plane.}
\end{figure}

\begin{figure}[H]
	\centering
	\begin{tikzpicture}		
		\pgftext[at=\pgfpoint{0cm}{0cm},left,base]
		{\inctrimpic[1]{images/motors/cm_render_45_3.pdf}};
		% ...
		
		\node (base) at (9, 0) [draw=none] {};
		\draw [line width=2pt, color=black] 
		(base)+(-6, 0) -- +(2, 0) ;
		\fill[pattern = north east lines]  ($ (base) + (-6, 0) $)  rectangle  ($ (base) + (2, -.5) $)  ;
		\draw[thick, color=orange] (base)+(-1,0) arc (180:140:1cm);
		\node at ($ (base) + (-1.1, 0.4) $) [draw=none] {\color{orange}$\alpha$};
		
		\node (G) at (5.2,3.7)
		[circle,draw=black,inner sep=2pt,fill=red]
		{};
		%		\draw[gray,dashed, thick,line width=1pt] (G) circle (2.3cm);

		\draw[line width=2pt,shorten <=6pt, color=blue]
		(G)+(4,-4) -- +(-4,4)
		node[draw=none,inner sep=0pt,fill=none] (V1)
		{};
		%		\node (X) at (7.1, 4.2)
		%		[draw=none]
		%		{};
		\draw[line width=2pt,arrows=->, color=red]
		(G) -- +(.3,2.8)
		node[below, inner sep=2pt,fill=black, circle] (CM)
		{};
		\node at (CM) [draw=none, above=0.2cm] {Centre of mass};
		
		%		\draw[line width=1.5pt, arrows=<->, color=green]
		%		(CM)+(0.1, 0.1) -- +(-2, -1.5) node[draw=none] (D) {}; %distance from axis of rotation
		\draw[line width=2pt, arrows=->, color=black]
		(CM) -- +(0, -3.5) node[draw=none, below] (F) {$F$}; %weight force
		\draw[line width=1.5pt, dashed, color=gray]
		(F) -- +(-2,2) node[draw=none] (vFh) {}; %vertical force helper
		\draw[line width=1.5pt, dashed, color=gray]
		(F) -- +(2,2) node[draw=none] (hFh) {}; %horizontal force helper
		\draw[line width=1.5pt, arrows=->, color={rgb:red,4;green,2;yellow,1}]
		(CM) -- +(1.8, -1.8) node[draw=none] (hF) {}; %horizontal component of the force
		\draw[line width=1.5pt, arrows=->, color=purple]
		(CM) -- +(-1.8, -1.8) node[draw=none] (vF) {}; %vertical component of the force

		\path (G)
		to node [below left=.2cm]
		{Axis of rotation} (G);
		\path (vF)
		to node [left]
		{$F_{\parallel}$} (vF);
		\path (hF)
		to node [below right=0.1cm]
		{$F_{\perp}$} (hF);
		%		\path (X)
		%		to node [left=0.2cm]
		%		{Lever arm} (CM);

		\draw[line width=2pt, color=red, arrows=->]
		(7.8, 2.7) -- +(1.5, 1.5) node[draw=none, left] (T) {\color{black}$T$};
	\end{tikzpicture}
	\caption{$\alpha$ is the angle between the \textit{top} plane and the ground. The weight force can be decomposed in a parallel and a perpendicular components, due to the angle of inclination $\alpha$. This force tries to rotate the gear, inducing a moment. The motor opposes this rotation, exercising a force $T$. }
	\label{fig:moment}
\end{figure}

To begin with, let's compute the \textbf{position of the centre of mass } of the camera. The dimensions that will be used are of the model Nikon D3300, the same used also for the tests. Its camera body can be roughly approximated with a parallelepiped, while the lens can be approximated with a cylinder. The body measures $124 \times 98 \times 76 mm$, while the the lens measures $73mm $ for the diameter and $79.5 mm$ in length.

The camera is mounted on top of a ball-head that can rotate in any direction, and form an angle $\beta$ with reference to the \textit{top} plane, but for now we will consider only the case where the camera sits parallel to the \textit{top} plane. We can also define an angle $\theta$ that describes how the camera in inclined with reference to the axis of rotation. $\beta$ is shown in \ref{fig:beta}, while $\theta$ in \ref{fig:theta}.

In general, the position of the centre of mass of $n$ elements is:

$$ CM = \frac{\sum_{i=0}^{n}x_i\cdot m_i}{\sum_{i=0}^{n} m_i} $$
\\
\\
where $x_i$ is the position of the element, and $m_i$ its mass.

Assuming the camera is oriented as in figure \ref{fig:xzplane}, and the origin $(0,0)$ of the reference system is in the leftmost point at the bottom of the camera, given the dimensions of the body and the lens, and their weight, the centre of mass is:

\begin{align*}
	x_{cm} & = \frac{115.8\cdot 265 + 38 \cdot 430}{265 + 430} \\ 
	z_{cm} & = \frac{36.5\cdot 265 + 49 \cdot 430}{265 + 430} 
\end{align*}

which holds:
\begin{align*}
	x_{cm} & = 67.6 mm \\
	z_{cm} & = 44.6 mm
\end{align*}

The position of the c.m. is useful to compute the distance from the centre of the underneath gear. 

The value just found assumes that the origin of the system is on the camera; let's assume the origin is now located at the centre of the gear. Since the axis of rotation, which passes through the origin in the gear, does not crosses also the point fixed as origin on the camera, there is an horizontal and vertical offset, as shown in figure \ref{fig:cmorigins}.

\begin{figure}[h]
	\centering
	\begin{tikzpicture}
		\pgftext[]{
			
		}
		
		\node (o1) at (-0.8, 0.7) [draw=black, circle, fill=cyan, inner sep=1.2pt] {};
		\node (o2) at (-0.15, -0.9) [draw=black, circle, fill=blue, inner sep=1.2pt] {};
		
		\draw [line width=1.5pt, color=cyan, arrows=->] (o1) -- +(0, 1) {};
		\draw [line width=1.5pt, color=cyan, arrows=->] (o1) -- +(1, 0) {};
		\draw [line width=1.5pt, color=blue, arrows=->] (o2) -- +(0, 1) {};
		\draw [line width=1.5pt, color=blue, arrows=->] (o2) -- +(1, 0) {};
		
		\node (cm) at (1, 1.3) [draw=black, fill=red, inner sep=1.6pt, circle] {};
		
		\node (o1t) at ($(o1) - (0, 0.2)$) [draw=none] {$O_1$};
		\node (o2t) at ($(o2) - (0.1, 0.3)$) [draw=none] {$O_2$};
		\node (cm1t) at ($(cm) + (0, 0.2)$) [draw=none, scale=0.8, color=cyan] {$(67.4, 44.6)_{O_1}$};
		\node (cm2t) at ($(cm) - (0, 0.2)$) [draw=none, scale=0.8, color=blue] {$(32.4, 123.6)_{O_2}$}; 
	\end{tikzpicture}
	\caption{The two origins used for the computations: $O_1$ is on the camera, $O_2$ is on the gear; this results in two different coordinates for the c.m.}
	\label{fig:cmorigins}
\end{figure}

The vertical offset is given from the height of the ball-head and the support between the ball-head and the gear. The horizontal offset is measured as the distance from the axis of rotation, which is the point where the camera is screwed at the ball-head, and the origin of the camera. 

So, the new centre of mass is:

\begin{align*}
	x_{cm} & = 67.4 - 35 \\
		   & = 32.4 mm \\
	z_{cm} & = 37.4 + 79 \\
		   & = 123.6 mm
\end{align*}

We can think of the system as a \textbf{pulley}: the camera tries to rotate it, while the motor applies an opposing force. When the system is parallel to the ground, the parallel component of the force with reference to the \textit{top} plane exercised by the camera is $0$; when the plane is perpendicular to the ground is maximum. We can approximate the camera with its centre of mass.

let's call this the \textbf{moment of force M}.

$$ M = \frac{\textnormal{distance between c.m. and centre of gear} \cdot F}{\textnormal{transmission  ratio}}$$

where $F$ is the weight force and \textit{transmission ratio} is the transmission ratio between the two gears. Only the parallel component of the weight force should be considered, $F_{\parallel}$, as shown in figure \ref{fig:moment}. So the final computation is:

$$ \frac{ \left[ (0.265 + 0.430)\cdot 9.81 \right] \cdot \sin\alpha \cdot 12.78}{\frac{126}{17}}$$
\\
$12.78$ is the distance in cm of the c.m. from the centre of the gear: $\sqrt{32.4^2 + 123.6^2}$. 

Considering various values of $\alpha$, this gives the following chart \ref{fig:momentchart}:

\begin{figure}[H]
	\centering
	\begin{tikzpicture}
		
		\begin{axis}[
			width=0.6\textwidth,
			title={Resistant moment in $N\cdot cm$},
			xlabel={Angle in deg $\alpha$},
			ylabel={Moment},
			xtick={0, 15, 30, 45, 60, 75, 90},
			xmin=0, xmax=90,
			axis lines = left,
			%			ytick={0, 250, 350, 500}
			]
			\addplot [ 
			domain=0:90, 
			color=red,
			mark=square, 
			samples = 7,
			nodes near coords, 
			xtick={0, 15, 30, 45, 60, 75, 90}, ]
			{((0.695 * 9.81)*sin(x)*12.78)/(126/17)}; 
			\addlegendentry{force moment}
			
			\addplot[
			domain=0:90,
			color=purple,
			dashed
			]{45};
			\addlegendentry{\( y = 45 N\cdot cm \)}
			
			\addplot[
			domain=0:90,
			color=cyan,
			dashed
			]{((45/4)};
			\addlegendentry{\( y = 11.25 N\cdot cm\)}
		\end{axis}
		
	\end{tikzpicture}
	\caption{This chart shows the moment generated by the camera at various inclination, the torque generated by the motor, and the torque generated by the motor divided by 4. }
	\label{fig:momentchart}
\end{figure}

The two horizontal lines, $y=45$ and $y=11.25$, are the torque of the motor. The second in particular is the moment divided by 4, for reasons that will be explained in the following subsection, since that number is obtained because of the technique used to drive the motor, \textit{microstepping}. The graph shows that, except above $\alpha = 75^{\circ}$ of inclination, the motor can move the camera. 

\begin{figure}[h]
	\centering
	\begin{tikzpicture}		
		\pgftext[at=\pgfpoint{0cm}{0cm},left,base]
		{\inctrimpic[1]{images/motors/cm_render_front_0.pdf}};
		% ...
		\node (G) at (6.4,3.8)
		[circle,draw=black,inner sep=2pt,fill=red]
		{};
		\draw[gray,dashed,line width=1pt] (G) circle (2.75cm);
		\draw [line width=1pt, color=black] 
		(G)+(-3, 0) -- +(2, 0) ;
		\draw[thick, color=orange] (G)+(-2,0) arc (180:105:2cm);
		\draw[thick, color=orange] (G)+(-1,0) arc (180:18:1cm);
		\draw[thick, color=orange] (G)+(-1.1,0) arc (180:18:1.1cm);
		\draw[line width=2pt,shorten <=6pt, color=blue]
		(G)+(0,4) -- +(0,-4)
		node[draw=none,inner sep=0pt,fill=none] (V1)
		{};
		%		\node (X) at (7.1, 4.2)
		%		[draw=none]
		%		{};
		\draw[line width=2pt,arrows=->, color=red]
		(G) -- +(-0.7,2.8)
		node[below, inner sep=2pt,fill=black, circle] (CM)
		{};
		\node at (CM) [draw=none, left=0.1cm] {Centre of mass};
		\node at (G) [draw=none, above left=1cm] {\color{orange}$\theta$};
		\node at (G) [draw=none, above left=0.3cm] {\color{orange}$\theta'$};
		
		\draw[line width=1.5pt, arrows=<->, color=green]
		(CM) -- +(0.7, 0)node[draw=none] (D) {};
		
		\path (V1)
		to node [above left=.6cm]
		{Axis of rotation} (G);
		%		\path (X)
		%		to node [left=0.2cm]
		%		{Lever arm} (CM);
		
		\draw[line width=1pt,arrows=->, color=red]
		(G) -- +(2.6,0.8)
		node[inner sep=1.5pt,fill=black, circle] (CMa)
		{}; %alternative center of mass
		\node at (CMa) [draw=none, right=0.1cm] {$CM'$};
		\draw[line width=1pt, arrows=<->, color=green]
		(CMa)+(0,0.1) -- +(-2.6, 0.1) node[draw=none] (D) {};
	\end{tikzpicture}
	\caption{This image represents the angles of the camera respect to the \textit{top} plane, if the camera is tilted on the ball-head on various position ($\theta$, $\theta'$). The tilt pushes the centre of mass of the camera closer or further from the axis of rotation. The double green arrow represents the horizontal distance of the c.m. from the axis of rotation. }
	%		Other values are available in table \ref{tab:angles}.}
\label{fig:theta}
\end{figure}

Until now, the angle $\beta$ of the camera on the ball-head used for the computation has been 0.
But we can consider any ball rotation: changing the angle on the camera brings the c.m. closer to the axis of rotation, or furthers it away, as shows figure \ref{fig:theta}.

Although these computations are not and will not be taken into consideration, it is still interesting to cite the possibility of improving the graph shown in \ref{fig:momentchart} by taking them into account, so a brief description of how to get these values is provided.

To compute the distance of the c.m. considering $\beta$, it is useful to introduce $\theta$, the angle between the camera and the \textit{top} plane. The c.m., as rotates around the centre of the ball in the ball-head, describes a circumference. Again, for simplicity, it is possible to only considering a 2D plane, and not a whole sphere. 

Knowing the position of the c.m. of the camera using the origin at the centre of the gear, it is possible to measure the distance between the c.m. and the centre of the ball in the ball-head. This gives the radius of the circumference introduced above. The radius is shown in figure \ref{fig:theta} (the red arrow) and more explicitly in figure \ref{fig:radius}.

The angle $\theta$ for $\beta = 0$ is given from:

$$\theta = \arcsin \frac{r_{\perp}}{\sqrt{r_{\perp}^2 + r_{\parallel}^2}} $$

where $r_{\perp}$ is the perpendicular component of $r$ w.r.t. the \textit{top} plane, or $r \cdot \sin \theta$, and $r_{\parallel}$ is the parallel component of $r$ w.r.t. the top plane, $r \cdot \cos \theta$. 

\begin{figure}[h]
	\centering
	\begin{tikzpicture}
		\pgftext[]{
			
		}
		
%		\node (o1) at (-0.8, 0.7) [draw=black, circle, fill=cyan, inner sep=1.2pt] {};
		\node (o2) at (-0.15, -0.9) [draw=black, circle, fill=blue, inner sep=1.2pt] {};
		
%		\draw [line width=1.5pt, color=cyan, arrows=->] (o1) -- +(0, 1) {};
%		\draw [line width=1.5pt, color=cyan, arrows=->] (o1) -- +(1, 0) {};
		\draw [line width=1.5pt, color=blue, arrows=->] (o2) -- +(0, 1) {};
		\draw [line width=1.5pt, color=blue, arrows=->] (o2) -- +(1, 0) {};
		
		\node (cm) at (1, 1.3) [draw=black, fill=red, inner sep=1.6pt, circle] {};
		
		\draw[arrows=->, line width=2pt, color=red] (o2) -- (cm) node[midway, below, scale=1.5, draw=none]{$r$} ;
		\draw[line width=1.5pt, arrows=->, color={rgb:red,4;green,2;yellow,1}]
		(cm) -- +(0, -2.1) node[draw=none, right] {$r_{\perp}$};
		\draw[line width=1.5pt, arrows=->, color=purple] (cm) -- +(-1.15, 0) node[left, draw=none] {$r_{\parallel}$};
		
	\end{tikzpicture}
	\caption{The distance from the centre of the gear and the c.m. of the camera; this also describe the radius of a circumference. In this figure are also shown its components.}
	\label{fig:radius}
\end{figure}

Finally, the torque is given by $r_{\parallel}\cdot F$, where $r_{\parallel}$ is the horizontal distance from axis, and $ F = m\cdot g = (430+265)\cdot9.81 $.

To conclude, it is possible to compute a more realistic moment of the force considering also a rotation $\theta$ of the camera: for different values of $\theta$ correspond different values of $r_{\parallel}$, i.e. the distance between the c.m. and the centre of the gear does not depend only on $\alpha$, but also on $\theta$. 

\subsection{Micro-stepping}

A stepper motor, such as the ones used in this project, is a motor that moves a shaft through the use of electromagnets. More specifically, there is a rotating, permanent magnet, called \textit{rotor}, and a \textit{stator}, which is a static part that is magnetized when the current passes through it \cite{steppermotors}. Every time the stator is magnetized, the rotor rotates. The rotation made by the rotor is called a \textbf{step}, and is a fixed amount of degrees; all the motors used for this project require 200 steps to make a complete rotation.
\\
\\
However, the time required for the big \textit{top} gear to make a complete rotation is more than $80,000$ seconds, a \textbf{sidereal day}, as explained in section \ref{sec:intro}. 

Considering the transmission ratio of the \textit{top} gears, which is $\frac{126}{17} \approx 7.4$, this means that $200 \cdot 7.4 $ steps of the small gear are needed to completely rotate the big gear. This rotation has to take the same amount of time of a sidereal day, i.e. 86164 seconds, which means that a step needs to take place every $\frac{86164}{200\cdot 7.4} \approx 58 $ seconds. But according to the \textit{500 rule}, this time is too long for the star tracker to be useful, because a star trail will appear during the wait time between the steps. 

Fortunately, there are some ways to augment the number of steps, reducing the wait time to an acceptable duration. 

To begin with, a \textbf{bipolar stepper motor}, such as the ones used in this project, has two stators, hence the motor is driven with two phases. There are several ways to drive the motor: \textit{single-phase step}, \textit{full-step}, \textit{half-step}. The core idea is that for every phase the current flows through one or two stator in a direction, then flows in the other rotor(s), then again in the first rotor(s) in the opposite direction and finally in the second rotor(s) in the opposite direction. The simplified schematic of a bipolar motor is shown in figure \ref{fig:schembipolar}, and the above modes are summarized in table \ref{tab:controlmodes}.

\begin{figure}[h]
	\centering
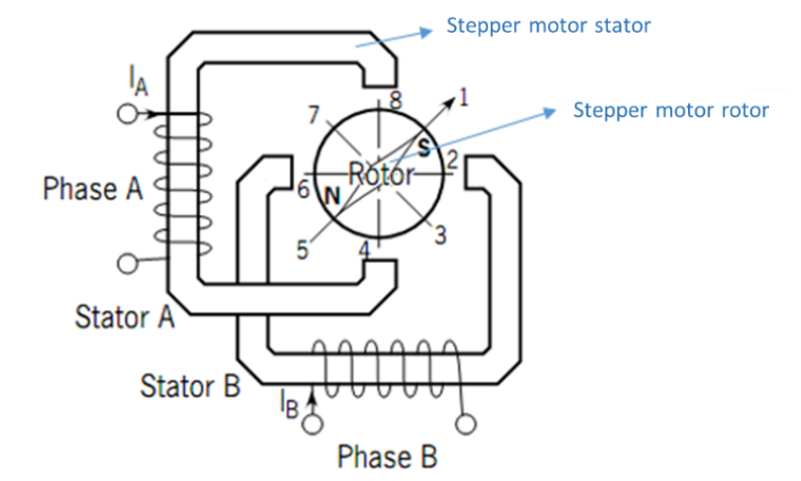
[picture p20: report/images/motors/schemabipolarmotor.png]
	
	\caption{Simplified Schematic of a Bipolar Stepper Motor \cite{steppermotors}.}
	\label{fig:schembipolar}
\end{figure}

\begin{figure}[h]
	\centering
%	\bgroup
	\def\arraystretch{1.5}
	\bfseries
	\begin{tabular}{|c|c|c|}
		\hline
		\thead{Stepping mode} & \thead{Sequence} & \thead{Electrical stepping position} \\
		\hline
		Single-phase step & $A > B > \bar{A} > \bar{B}$ & $8 > 2 > 4 > 6$\\
		\hline
		Full step & $AB >  \bar{A} B > \overline{AB} > A\bar{B}$ & $1 > 3 > 5 > 7$ \\
		\hline
		Half-step & $AB > B > \bar{A}B > \bar{A} > \overline{AB} > \bar{B} > A\bar{B} > A $ & $1>2>3>4>5>6>7>8$ \\
		\hline
	\end{tabular}
	\caption{Stepper Motor Control Modes \cite{steppermotors}}
	\label{tab:controlmodes}
	
\end{figure}

If the half-step mode is used, the steps needed double, allowing to halve the wait time: $\frac{58}{2} = 29$ seconds. 

But it is also possible to use the \textbf{microstepping} technique, which consists of dividing a single step in multiple steps: for example, using two microsteps the number of steps is once again halved and the wait time can be brought down to about 14 seconds. 

Normally, the impulse to the stator is digital, meaning there is current or there is not. With microstepping, the impulse is sent in a wave form, thus the step is gradual as the amount of current increases or decreases. A sinusoidal wave form is obtained through \textbf{PWM}, pulse-width modulation \cite{microstepping}. 
\\
\\
Microstepping solves the problem of obtaining a smooth, slow rotation, but since a smaller amount of current is used, less torque is produced by the motor. For simplicity, let's assume that the torque is linearly proportional to the amount of current \footnote{This is a generous assumption, since it is not obvious: see \cite{torquevoltage}.}. Fortunately, according to the computation of the previous subsection, as shown in chart \ref{fig:momentchart}, even diving by 4 - i.e. 4 microsteps - the amount of torque is still enough to move the camera below $75^{\circ}$ of inclination. Thus, a \textbf{2 microsteps} step can be safely used. 

\newpage
\section{Electronics}
In this section, all the electronic components, the electronic scheme and some energy considerations are discussed. 

The table below \ref{tab:elecsummary} provides a summary of all the components used, excluding the motor, which specifications where introduced in table \ref{tab:topseq}.

\begin{table}[H]
	\centering
	\def\arraystretch{1.5}
	\begin{tabularx}{\linewidth}{|X|c|c|X|}
		\hline
		\textbf{Name} & \textbf{Voltage} & \textbf{Current} & \textbf{Description} \\
		\hline
		Raspberry Pi 3B+ & 5V & 2.5A & The Raspberry connects all the sensors actuators, and provides computation capabilities. \\
		\hline 
		GY-521 MPU6050 & 3V & 3.9mA & accelerometer to read \textit{top} plane inclination \\
		\hline
		MT3608 & 2V-24V & 2A & DC-DC step up booster \\
		\hline
		u-blox NEO-6M GPS & 3V & 45mA & gps chip to get date and position \\
		\hline
		Adafruit ICM20948 & 1.8V & 3.11mA  & IMU, used to orient the startracker towards the north \\
		\hline
	 	L298N DC motor driver & 5V & 4A & motor driver (operates at 5V, can manage an input voltage to drive the motor up to 48V) \\
	 	\hline
 		L9110 H-bridge module & 2.5V & 1.6A & motor driver \\
	 	\hline
	 	led & 2V & 20mA & led \\
	 	\hline
	 	resistor & & & $560 \Omega$ resistor for the led \\
	 	\hline
	 	on-off button & & & button to read digital input \\
	 	\hline
	 	unipolar switch & max 250V & 2A & on-off switch between battery and motors \\
	 	\hline
	 	TP4056 & 4.5V-5.5V & 1A & microusb battery charger module \\
	 	\hline
	 	LIPO-2200mAh & 3.7V & & battery for the motors \\
	 	\hline
	\end{tabularx}
	\caption{Summary of all the electronic components used, except the motors.}
	\label{tab:elecsummary}
\end{table}

\begin{figure}[H]
	\centering
	
	\caption{The electronic scheme.}
	\label{fig:elecfullscheme}
\end{figure}

Given the nature of the simple logic required by the sensors and actuators, a microcontroller such as an Arduino would have been a more suitable choice; it would have also provided additional improvements such as less energy consumption and a finer control, due to the lack of an operating system that can introduce some lag. 

However, the Raspberry was already available to me, so a microcontroller was an additional purchase that could have been avoided.  Furthermore, using the Raspberry it is possible to develop an additional image-based alignment technique, for which a microcontroller is not suitable, due to the lack of processing power. In this sense, the raspberry makes the project more "future proof". 

While the sensors, the led-resistor and the on-off button are directly attached to the Raspberry, the motor circuitry is slightly more complicated. 

There are two smaller motors, the Nema 17HS4023, and a bigger one, the 17HS15, as showed in table \ref{table:motor}. Since the first motor require less voltage, they are attached to drivers (L9110) which are connected directly to the battery. 

The second motor, however, is attached to a DC-DC converter that steps up the output voltage of the battery, to around 12V. So, the battery is connected to this module, which is connected to a more powerful driver (L298N) which is finally attached to the motor. A second DC-DC converter is also connected from the battery to the driver; while the first provides the energy for the motors, the second powers the driver itself. 

The battery is connected to a charger circuit (TP4056); hence, the motor drivers are not directly connected to the battery as previously stated, but are actually connected to this charger circuit. 

These connections are summarized in figure \ref{fig:batterycircuit}.

\begin{figure}[h]
	\centering
	\begin{tikzpicture}
		\pgftext[]{
			
		}
		\draw[line width=1pt, blue] (1.2,-1.6) ellipse (0.8 and 1.1);
		\draw[line width=1pt, green] (3.3,-1.6) ellipse (1.2 and 0.8);
		
	\end{tikzpicture}
	\caption{Battery and motor electric circuit: the battery is connected to a charger module, circled in \textcolor{blue}{blue}; from here, 4 red wires exit and are connected to the two DC-DC step up modules, one of which is circled in \textcolor{green}{green} (the other one is below), and the two motor driver at the top of the image. The charger module, DC-DC and motor drivers are also all connected through the on-off switch at the centre of the image, to disconnect the load from the battery. Finally, the DC-DC modules are connected to another motor drive, not included in this image.}
	\label{fig:batterycircuit}
\end{figure}

\subsection{Communication protocols}\label{sec:communication}
The various sensors such as the gps and the IMU modules are connected directly to the Raspberry, to which communicate with 2 protocols:

\begin{itemize}
	\item \textbf{I2C protocol};
	\item \textbf{UART protocol}.
\end{itemize}

The Raspberry provides a bus for each of these communication protocol: I2C bus is accessible through GPIO pins 2 and 3, while UART through pin 14 and 15. 

Here there is the list of each electronic component and its communication protocol:
\begin{itemize}
	\item GY-521: I2C;
	\item NEO 6M GPS: UART;
	\item Adafruit ICM20948: I2C.
\end{itemize}

The rest of the electronic components (led, motor drivers...) are controlled only setting on or off the pins to which they are connected.

However, there are two I2C devices and one bus; but in the Raspberry Pi, is possible to define a software I2C bus using two generic GPIO pins \cite{i2cadafruit}. Thus, while the Adafruit chip is connected to the GPIO pins 2 and 3, the GY-521 is connected to the GPIO pins 23 and 24. 

This is obtained through the \textbf{Device Tree overlay feature} of the Raspberry's firmware. An overlay purpose is to modify the kernel live tree; the device tree describes the hardware of a system, using a tree data structure. To configure the overlays, the file \texttt{/boot/config.txt} must be edited. In the case of the software I2C, two lines were added:

\begin{lstlisting}[language=Bash, caption={Additional lines in \texttt{/boot/config.txt} to add a software I2C overlay.}]
dtoverlay=i2c-gpio #define the overlay
dtoverlay=i2c-gpio,i2c_gpio_sda=23,i2c_gpio_scl=24 #specify the pins
\end{lstlisting}

\subsection{Energy power computation}
Knowing how much energy the system consumes, allows to estimate the battery duration, hence for how long it is possible to use the system.

To begin with, let's compute how much power the battery can provide working for 1 hour:

$$ P = V\cdot I \cdot 1h  = 3.7 \cdot 2200Ah = 8.14 Wh $$

Using the same method, it is possible to compute the power required by the motors attached to the battery.

The first motor, the bigger one, can be run at $1.5A$, and $12V$, thus giving $18Wh$.

The second and the third run at $1A$ and $3.7V$ each, which gives $3.7Wh$; multiplying by 2 the total is $7.4Wh$. 

The driver for the bigger motor, the L298N, runs at around $36mA$ and $5V$, which gives $0.18Wh$; the other two drivers are not alimented through to the battery, but the boards are powered by the Raspberry.

So, the total time the battery can operate under this load is given from:

$$ \frac{8.14}{18 + 7.4 + 0.18} \cdot 60 \approx 19 \textnormal{minutes} $$

Now, assuming that the DC-DC modules have an efficiency of 80\% \cite{mtspecs} to boost the input voltage to $12V$, 
the total is $19\cdot 0.8 = 15.2 $ minutes. Since the second module output is $5V$, its efficiency should be around 90\%, resulting in $15.2\cdot 0.9 = 16.7$ minutes, which is enough for taking e.g. two 5 minutes exposure pictures.

\subsubsection{Problems of using MT3608 modules}
These modules are DC-DC voltage booster: their purpose is to increase the input voltage. But this is achieved decreasing the current: this means that the bigger motor is driven with a much low current than the needed $1.5A$ in its specification. In fact, stepper motor torque is proportional to the current, and stepper motors should be driven with constant current \cite{steppermcurrent}.

According to \cite{mteffspec}, which tested the efficiency of the module, applying a $2A$ input resulted in a $0.4A$ of output, or about 20\% of the input, with the module configured to boost $5V$ to $12V$.

\subsubsection{Raspberry Pi power consumption}
Assuming the Raspberry Pi 3B+ consumes around $5W$ while not in idle \cite{powerbenchmark}, it is possible to estimate how much power requires considering also the attached electronic components. 

For all the components, the voltage and current are listed, and the computation is straightforward using the formula $P=V\cdot I$ introduced before:

\begin{itemize}
	\item GY-521: $3 \cdot 0.0039 = 0.012W$
	\item NEO-6M: $3 \cdot 0.045 = 0.135W$
	\item Adafruit ICM20948: $1.8 \cdot 0.0031 = 0.006W$
\end{itemize}

The total of the watts above is $0.513W$. There is another component though, the $560\Omega$ resistor and led, for which another two formulae are needed:

$$ P = \frac{V^2}{R} \qquad\qquad I = \frac{(V_i - V_o)}{R}$$

$R$ is known, is the resistance of the resistor and its value is $560\Omega$; $V_i$ is the voltage supplied from the Raspberry, $5V$, while $V_o$ is the voltage at which the led operates: $2V$. Thus, the value at which the led operated, I, is $\frac{5-2}{560} = 5.3mA$.

From this value, it is possible to compute the power used by the led: $2 \cdot 0.0053 = 0.011W$ and the resistor: $P = \frac{(5-2)^2}{560} = 0.016W$.

Thus, the total power consumption for the raspberry is $\approx 5.53 W$.

\subsection{Magnetic calibration}\label{sec:iron_calib}
A magnetometer is a sensor that can measure the strength of a magnetic field. Unfortunately, what is actually measured is a combination of all the local magnetic fields; this is particularly problematic if the magnetometer is needed to find the Earth's magnetic north. 

\begin{figure}[H]
	\centering
	\subfigure[No distortions]{
		\begin{tikzpicture}
   			\begin{axis}[
				width=0.45\textwidth,
				xmin=-2, xmax=2,
				ymin=-2, ymax=2,
    			minor tick num=1,
				grid=both,
				grid style={line width=.05pt, draw=gray!10},
				major grid style={line width=.1pt,draw=gray!50},
				axis lines=middle,
				]
				
				\coordinate (O) at (axis cs: 0, 0); 
				\node[fill=white,circle,inner sep=0pt] (O-label) at ($(O) - (25,25)$) {$O$};
				\draw[color=blue] (O) circle [radius=100];
				
			\end{axis}
		\end{tikzpicture}
	}
	\subfigure[Hard and soft iron distortions]{
		\begin{tikzpicture}
			\begin{axis}[
				width=0.45\textwidth,
				xmin=-2, xmax=2,
				ymin=-2, ymax=2,
				minor tick num=1,
				grid=both,
				grid style={line width=.05pt, draw=gray!10},
				major grid style={line width=.1pt,draw=gray!50},
				axis lines=middle,
				]
				\coordinate (O) at (axis cs: 0, 0); 
				\coordinate (C) at (axis cs: 0.7, 0.9); 
				\node[fill=white,circle,inner sep=0pt] (O-label) at ($(O) - (25,25)$) {$O$};
				\draw[color=blue, rotate=45] (C) ellipse({1cm} and {0.4cm});
				\draw[color=red, rotate=45] (C) -- +( 1cm,  0)     {};
				\draw[color=red, rotate=45] (C) -- +(-1cm,  0)     {};
				\draw[color=red, rotate=45] (C) -- +(   0,  0.4cm) {};
				\draw[color=red, rotate=45] (C) -- +(   0, -0.4cm) {};
				]
			\end{axis}
		\end{tikzpicture}
	}
	\caption{Effects of the magnetic disturbances: the second figure is shifted from the centre (hard iron), and forms an ellipse (soft iron distortion).\\}
\end{figure}

If the magnetometer is rotated around an axis, and the read magnetic field is plotted on a 2D plane, the plot should form a circle, assuming no disturbances are present. 
There are two types of magnetic disturbances \cite{vectornav}:
\begin{itemize}
	\item \textbf{soft iron}: this type of distortion is commonly caused by metals and other sources such as batteries; they tend to stretch the plot, making it elliptical;
	\item \textbf{hard iron}: these disturbances come from other magnetic fields nearby, and cause the plot to be off-centre.
\end{itemize}

After collecting data about the magnetic field around the magnetometer rotating it, it is possible to analyse the data to compute the necessary correction to calibrate the magnetometer, and allow it to find the magnetic north more precisely. After computing these distortions, a compensation model can be constructed to account for hard and soft iron disturbances:

$$ m_c = S_I(\tilde{m} - b_{H_I}) $$

where:

\begin{itemize}
	\item $m_c$: the vector $(m_{c_x}, m_{c_y}, m_{c_z})$ of the compensated magnetic field;
	\item $\tilde{m}$: the vector $(\tilde{m}_x, \tilde{m}_y, \tilde{m}_z)$ read in one point at a given instant that we are compensating;
	\item $S_I$: the matrix of the soft iron distortion;
	\item $b_{H_I}$: the matrix that represents the translation from the origin, due to the hard iron disturbances. 
\end{itemize}

More explicitly, $m_c$ is calculated as:

	\[ \left[ \begin{array}{c}
	m_{c_x} \\
	m_{c_y} \\
	m_{c_z} \end{array} \right]
	 = 
	\left[ \begin{array}{ccc}
	C_{00} & C_{01} & C_{02} \\
	C_{10} & C_{11} & C_{12} \\
	C_{20} & C_{21} & C_{22} \end{array} \right]
	\left[ \begin{array}{c}
	\tilde{m}_x - b_{H_0} \\
	\tilde{m}_y - b_{H_1} \\
	\tilde{m}_z - b_{H_2} \end{array} \right]
	\] 

$SI$ and $b_{H_I}$ can be computed through several programs; for this project, \cite{calibsw} was used.

\begin{figure}[H]
	\centering
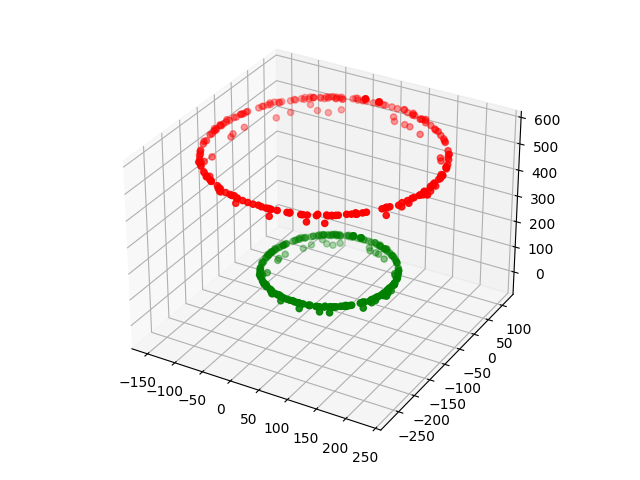
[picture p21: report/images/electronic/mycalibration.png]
	
	\caption{Results of the calibration with the sensor used in the project. The red dots are the original readings, the green are the compensated values.\\}
\end{figure}

\newpage	
\section{Software}\label{sec:software}
This section is dedicated to explain the software architecture and show some implementation details. 

There are two components: a \texttt{systemd} service that starts the main software, and the core of the software, written in Python. 

The \textbf{main software} is composed of 5 files: 
\begin{enumerate}
	\item \texttt{main.py}: in this file, the values of the sensors (button, gps, ...) are read and the actuators (the motors) are used accordingly
\end{enumerate}

The other 4 files are auxiliary files, inside the folder \texttt{lib}:

\begin{enumerate}
	\setcounter{enumi}{1}
	\item \texttt{motors.py}: contains the functions to run the motors;
	\item \texttt{gps.py}: contains the function to receive and parse data from the gps sensor;
	\item \texttt{compass.py}: reads the magnetometer data and computes the angle between the current heading and the north;
	\item \texttt{accel.py}: reads the data from the accelerometer positioned on the \textit{top} plane to check its tilting angle. 
\end{enumerate}

The use of the star tracker is fairly simple: first of all, it needs to receive its gps location and its orientation, after which the button can be pressed by the user to start the plane tilting and at last the actual tracking. But these operation do not need to be run sequentially, and for some it is actually impossible: the user can press the button at any time, so they should be run with some form of concurrency, that allow the star tracker to perform its operations while listening for user input. 

The adopted solution is to use the \textbf{asynchronous} paradigm, made possible in Python by the relatively new \texttt{asyncio} module and \texttt{async/await} keywords. This paradigm is particularly suitable for this use case, since it is dominated by various I/O operations rather than cpu-bound ones, where instead threading programming is better \cite{asyncpython}. In this paradigm a single thread is used, where different \textit{coroutines} are executed concurrently: the coroutines are a central idea of this design, and can be considered as functions that are able to be paused and resumed later. In a typical execution, then, there are different coroutines, and only one is running at a time: when the running coroutine has nothing to do, because e.g. it's waiting an output operation to finish, it can suspend its execution and another will be resumed.

\subsection{\texttt{main.py}}

After having introduced the paradigm used, \texttt{main.py} will be analysed in more detail. This file has 5 tasks, as the listing \ref{lst:maintasks} shows:

\begin{lstlisting}[language=PythonPlus, label={lst:maintasks}, caption=main tasks]
async def main():
  task_button = asyncio.create_task(listen_button()) 
  task_gps_compass = asyncio.create_task(listen_gps_compass())
  task_tracking = asyncio.create_task(tracking())
  task_accel = asyncio.create_task(listen_accel())
  task_led = asyncio.create_task(control_led())
  await asyncio.gather(task_button, task_gps_compass, task_tracking, task_accel, task_led) 
\end{lstlisting}

These tasks wait for some conditions to be met; for example, \texttt{task\_led} turns on the led when the star tracker is correctly oriented towards north. To know when the conditions are met, every task checks some global variables, show in listing \ref{lst:globvar}; if they are \texttt{False/None/empty}, the tasks pauses for 1 second. \texttt{task\_button}, \texttt{task\_tracking} and \texttt{task\_led} run forever, while \texttt{task\_gps\_compass} and \texttt{task\_accel} return after their job is done. 

\begin{lstlisting}[language=PythonPlus, label={lst:globvar}, caption=Global variables used to coordinate the tasks]
is_running = False      # status of the star tracker (running/not running)
is_ready_1 = False      # wether the star tracker points to north and we have gps data
is_ready_2 = False      # wether the star tracker is ready to track (in the correct position)
\end{lstlisting}

Figure \ref{fig:mainsequence} shows the "interaction", or to be more precise, the coroutines running during a typical flow of execution.

\begin{figure}[h]
	\centering
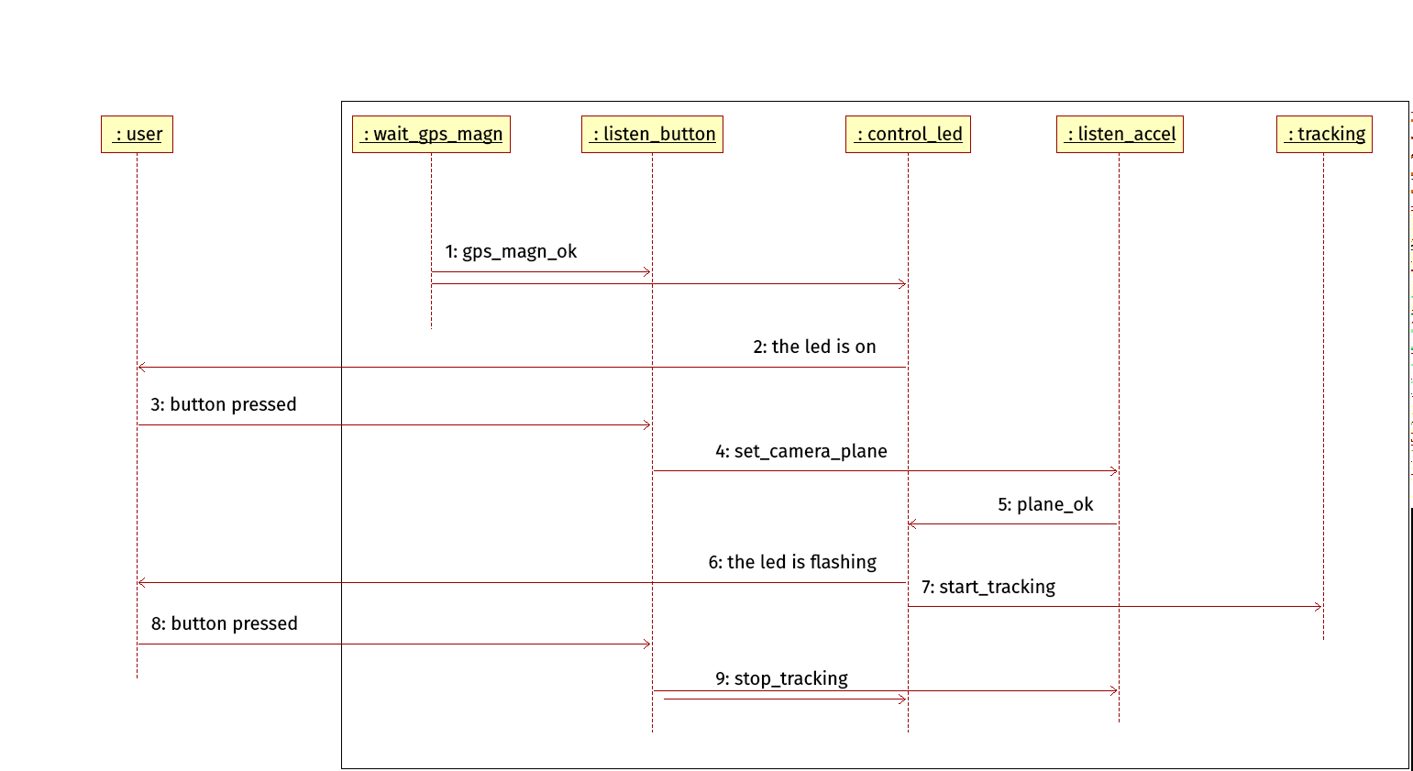
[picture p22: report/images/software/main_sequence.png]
	
	\caption{Typical flow of execution. The objects are the coroutines.}
	\label{fig:mainsequence}
\end{figure}

In the following paragraphs is explained what the coroutines do.

\paragraph{wait\_gps\_magn} This coroutine, which is actually called \texttt{listen\_gps\_compass} but shortened in \ref{fig:mainsequence}, listens for the gps signal; after having received the location and the current date, these information can be used to point the star tracker towards north: in fact, the actual geographic north is shifted from the magnetic north, and this phenomenon is called \textit{declination} (see section \ref{sec:mag_decl}). This depends on the location and date. The library \texttt{wmm2020} \cite{wmm2020} is used to compute the declination angle.

\begin{lstlisting}[mathescape, language=PythonPlus, label={lst:waitgps}, caption=Extract from the \texttt{listen\_gps\_compass} coroutine: it makes the base motor vibrate according to the actual heading.]
if  _compass < 180: #we are, e.g., at 40${^\circ}$ from north and must turn anticlockwise
	print("we should turn a bit anticlockwise, vibrate once for", _compass/90, "seconds")
	# let's signal it to the user with a vibrations:
	motors.vibrate("z", _compass/90) #vibration in seconds: 180 = 2 sec, 90 = 1 sec etc.
	
	time.sleep(3) #time for the user to make the adjustement
else: #we are, e.g. 330${^\circ}$ = 30${^\circ}$ from north and must turn clockwise
	print("we should turn a bit clockwise, vibrate twice for", _compass/180, "seconds each")
	# let's signal it to the user with two vibrations:
	motors.vibrate("z", (360 - _compass)/180) #it's like (_compass/90)/2
	time.sleep(0.5)
	motors.vibrate("z", (360 - _compass)/180) #it's like (_compass/90)/2
	
	time.sleep(3) #time for the user to make the adjustement
\end{lstlisting}

The motor inside the \textit{base} vibrates according to how many degrees the rest of the star tracker needs to rotate: if it needs to rotate anticlockwise, the duration in seconds is given from $\frac{\textnormal{actual heading}}{90}$: the maximum duration is 2 seconds when the actual heading is $180^\circ$, and decreases as the angle gets close to 0. 

If the actual heading is greater than $180^\circ$, and the rotation can be done clockwise, it is signalled through the same mechanism, but with two vibration, which duration is computed through the same mechanism and divided by two; so the maximum of each vibration is 1 second. 

The user has then some time to make the adjustments.

This coroutine sets the variable \texttt{is\_ready\_one}. 

Note that the position given from the gps and the angle given from the magnetometer are read multiple times and averaged.

\paragraph{listen\_button} This coroutine listens for button input by the user. If the global variable \texttt{is\_ready\_1} is true, a button press above 3 seconds will set \texttt{is\_running} to true, otherwise to false. If the pressing lasts more than 10 seconds, the Raspberry will shut down.
\paragraph{control\_led} This coroutine checks the global variables \texttt{is\_ready\_one} and \texttt{is\_ready\_two} to know at which state the star tracker is. If both are false, the led is turned off; if the first one is true, the led is turned on; if both are true, it first blinks sequentially faster, and each blink duration derives from the Fibonacci's sequence: $\sum_{i=1}^{12}\frac{1}{fib(i)}$, which gives the user around 9 seconds to press the shutter button on the camera; and then blinks twice every 30 seconds, to signal that the tracking is in progress. 
\paragraph{listen\_accel} This coroutine waits until the global variables \texttt{is\_ready\_one} \texttt{is\_running} are true; then, after reading the tilt of the \textit{top} plane from the accelerometer installed there, runs the motor for the necessary steps and waits 15 seconds before reading the value again. This is done because the user may want to change the camera position after installing it, altering the tilt. If two consecutive reads report the correct value, the variable \texttt{is\_ready\_two} is set to true.

As in the gps/magnetometer case, the values are read multiple times and averaged. 

The number of steps necessary to move in the correct position depends on the gear ratio and the stepping angle, which is $1.8^\circ$, as shown in listing \ref{lst:steps}. The target angle is given from the latitude, in turn obtained from the gps. 

\begin{lstlisting}[language=PythonPlus, label={lst:steps}, caption=The computation inside \texttt{listen\_accel} to compute the steps needed to move in the correct position the \textit{top} plane.]
distance = gps_data[0] - _tilt # tilt is the actual tilt - from the averaged readings
# ...
rot2  = distance*gear_ratio2
step1 = abs(int((rot2*gear_ratio1)/1.8))
print("accel: we are at tilt", _tilt, "and need to go to", gps_data[0])
print("accel:", step1, "steps needed to position correctly - distance is", distance)
if distance > 0:
	print("accel: I need to move clockwise")
	motors.move("x", step1, clockwise=True)
else:
	print("accel: I need to move anticlockwise")
	motors.move("x", step1, clockwise=False)
\end{lstlisting}

\paragraph{tracking} This coroutine checks the variable \texttt{is\_ready\_two} and, when it is true, runs the bigger motor to move the camera. Before running, it waits 10 seconds, during which concurrently the led is flashing to alert the user. 
\\
\\
In the following subsections, the other files will be analysed. 

\begin{figure}[h]
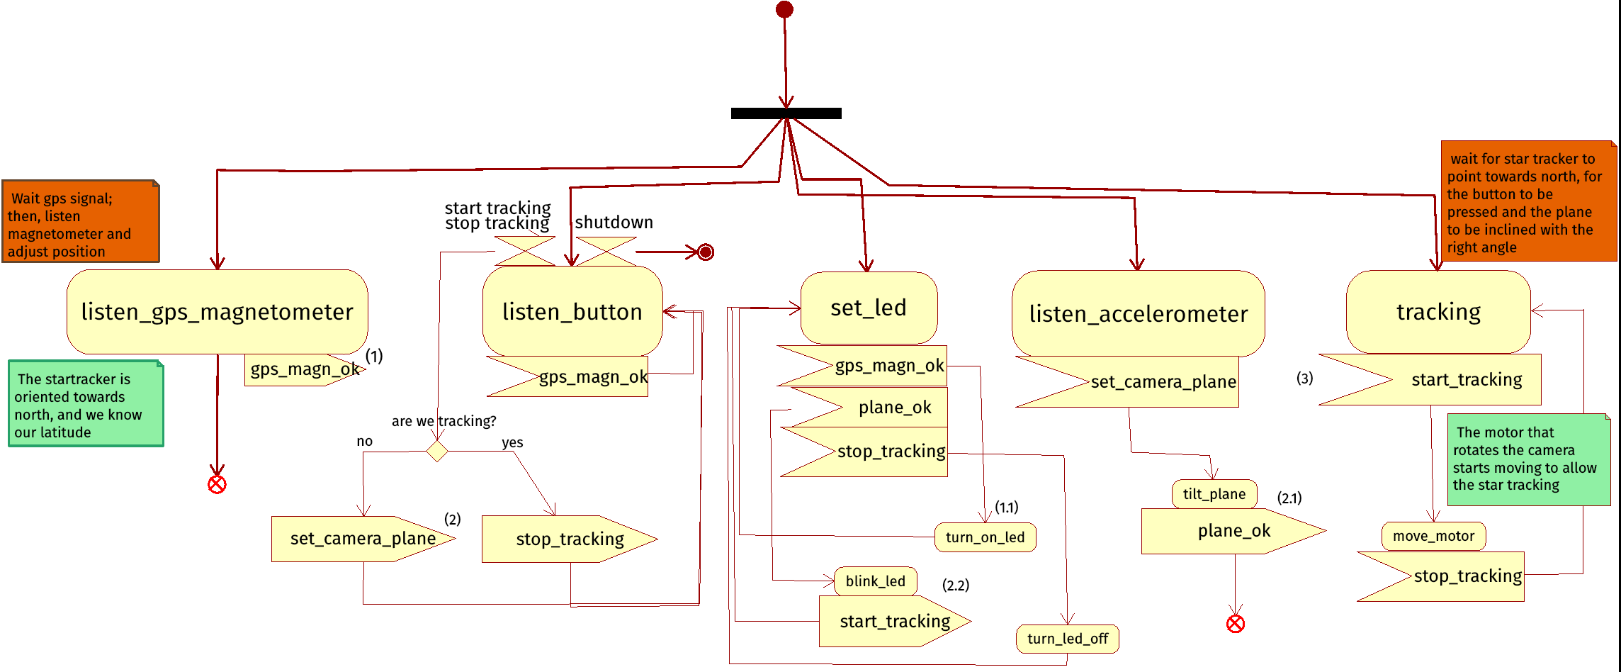
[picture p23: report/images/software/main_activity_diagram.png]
	
	\caption{The activity diagram for \texttt{main.py}: \textbf{1.} the star tracker receives the gps position and is headed towards north; \textbf{1.1.} the led is turned on to nofify the user; \textbf{2.} the user presses the button, \textbf{2.1.} the \textit{top} plane is tilted and \textbf{2.2.} and the led starts blinking; \textbf{3.} after a timeout, during which the led blinks, the biggest motor starts moving to allow the actual tracking.}
\end{figure}

\subsection{\texttt{motors.py}}
This file is responsible for the movement of the motors. They are identified with three letters: \texttt{x} for the one on the \textit{middle} part, \texttt{y} identifies the one in the \textit{top} plane and \texttt{z} is for the one \textit{base} part. The letters refer to the axis on with the rotation occurs.

Since these motors are stepper motors, it is possible to move them when the right sequence of signal is sent to their driver. They are hence driven using Raspberry's GPIO, which are set to output a signal or not output a signal, as shown in listing \ref{lst:motmove}: the motors have two coils, when the current passes in one direction in one coil, it creates a magnetic field; when the current passes in the same coil in the other direction, the magnetic filed is inverted. This makes the stator move. So, the variable \texttt{step\_sequence} contains the list of pins that need to output the signal (can be more than one at a time) for a step to occur. 

\begin{lstlisting}[language=PythonPlus, label={lst:motmove}, caption=The main code for the function \texttt{move} in \texttt{motors.py}.]
def move(motor, steps, clockwise=True):
	# ...
	while True:
	for pin_list in step_sequence:
		for pin in pins:
			if pin not in pin_list:
				GPIO.output(pin, True)
			else:
				GPIO.output(pin, False)
			steps -= 1
			if steps < 0:
				return
			print("steps remaining in move:", steps, end="\r")
			time.sleep(WAIT)
\end{lstlisting}

A global variable, \texttt{motor\_pins}, specifies which pins control which motor, and in what order they must be used. Then, according to how the motor needs to be driven, a step sequence is generated, as shown in listing \ref{lst:stepsequence}:

\begin{lstlisting}[language=PythonPlus, label={lst:stepsequence}, caption=Generation of a step sequence to move a motor inside the \texttt{move} function.]

step_sequence = list(range(4))

pins = copy.deepcopy(motor_pins[motor]) # this is equal to e.g. [1,2,3,4]

if not clockwise:
	pins.reverse()

step_sequence[0] = [pins[0], pins[1]]
step_sequence[1] = [pins[1], pins[2]]
step_sequence[2] = [pins[2], pins[3]]
step_sequence[3] = [pins[0], pins[3]]

\end{lstlisting}

There are three main functions in this file. 

\paragraph{lock\_motor} Set the first two pins of the given motor to true, and the other to false. This has the effect of "locking" the motor in place.

\paragraph{move} This function is shown in the above listings, \ref{lst:motmove} and \ref{lst:stepsequence}. It can move a given motor for a given number of steps; there is another input variable to specify if the movement should be clockwise or counter-clockwise. 

\paragraph{move\_microstep} This function is a variant of the \texttt{move} function. The idea behind it is, instead of setting the output in a binary fashion (signal or not signal), use the \textbf{pulse width modulation} technique, which allows to simulate an analog signal. This makes the rotation smoother, in \textbf{microstep}, instead of normal $1.8^\circ$ steps. This is done to allow a longer time to complete a rotation, since a really slow rotation is needed to allow the star tracking. 

The duration of a step is computed considering the step sequence, which is longer than the \texttt{move} one, the ratio between the gears and the \textbf{sidereal day} duration in seconds, which is the total time during which the complete rotation must take place. Listing \ref{lst:sidcomput} shows it. 

\begin{lstlisting}[language=PythonPlus, label={lst:sidcomput}, caption={\texttt{move\_microstep} function, showing the computations for how much time wait between a step and another.}]
wait_between_steps = (sidereal_day/(200*4*gear_ratio)) - wait_time #here 50 comes from 200/4
\end{lstlisting}

200 is the number of steps to make a rotation (since each step is $1.8^\circ \Rightarrow 1.8*50=360$), 4 is the number of microsteps (technically every step is composed of 2 microsteps, but since the step sequence is longer, 400 steps are needed). This gives a wait time of about 14 seconds.

If $A$ is coil in which the current flows in a certain direction and $\bar{A}$ is when the current flows in the opposite direction, and the same goes for the other coil $B$, then the step sequence is given from $AB > B > \bar{A}B > \bar{A} > \overline{AB} > \bar{B} > A\bar{B} > A$. 

To conclude, \ref{lst:pwm} shows another snippet of code from the function $move\_microstep$, that shows how the pwm is implemented:

\begin{lstlisting}[language=PythonPlus, label={lst:pwm}, caption=The use of the pwm capability of the Raspberry in the \texttt{move\_microstep} function.]
async def move_microstep(motor, steps, sleep=False, clockwise=True):
	# ...
	wait_between_steps = (sidereal_day/(200*4*gear_ratio)) - wait_time 

	pin_pwm_1 = GPIO.PWM(pins[0],frequency)		#create PWM instance with frequency
	# ...
	pin_pwm_1.start(0)				#start PWM of required Duty Cycle 
	pin_pwm_2.start(0)				#start PWM of required Duty Cycle 
	pin_pwm_3.start(0)				#start PWM of required Duty Cycle 
	pin_pwm_4.start(0)				#start PWM of required Duty Cycle 

	first_time=True
	while True:
		for duty in range(0, max_pwm_value+1, resolution):
		
			pin_pwm_1.ChangeDutyCycle(duty)
			time.sleep(wait_time)
			if sleep:
				await asyncio.sleep(wait_between_steps)
		# ...
		
\end{lstlisting}

\subsection{\texttt{gps.py}}
This file is responsible for handling the gps module. Since the communication with this chip happens through the serial protocol, to get data from the gps this communication must be initialized. The data is then parsed through a library, \texttt{pynmea2}. This is because gps send data in the \textit{NMEA} standard \cite{gps_nmea}. 

The listing \ref{lst:gps} shows the important parts of the code.

\begin{lstlisting}[language=PythonPlus, label={lst:gps}, caption=Code for the \texttt{gps.py} file. The serial port initialization and data parsing are shown.]
def _port_setup(port):
	ser = serial.Serial(port, baudrate=9600, timeout=2)
	return ser

def _parseGPSdata(ser):
	keywords = ["$GPRMC","$GPGGA"]
	gps_data = ser.readline()
	gps_data = gps_data.decode("utf-8")  # transform data into plain string
	try:
		nmeaobj = pynmea2.parse(gps_data)
	except Exception as e:
		print(e)

	if len(gps_data) > 5:  # Check to see if the GPS gave any useful data
		if gps_data[0:6] in keywords:   # Check t see if the message code
			try:
				gps_msg = pynmea2.parse(gps_data)
				lat = gps_msg.latitude
				lng = gps_msg.longitude
				alt = gps_msg.altitude 
				date = gps_msg.timestamp
				return (lat,lng,alt,date)
			except:
				return None
	return None
\end{lstlisting}

\subsection{\texttt{compass.py}}

\begin{floatingfigure}[r]{0.35\linewidth}
	
	\caption{arcsine and arccosine cannot tell the difference between some angles, e.g. the arcsine for $x$ and $x+90^\circ$ is the same.\\}
\end{floatingfigure}

This file is responsible for the communication with the magnetometer sensor. Since it is an Adafruit product, there is a fairly easy to use library, \texttt{adafruit\_icm20x}, which handles all the communication. The data can be obtained simply calling the \texttt{icm.magnetic} member of the class \texttt{ICM20948}, which stores the magnetic field along the x, y and z axis: \texttt{mx, my, mz}. 

Then, this data is used to correct for hard and soft iron disturbances, as explained in section \ref{sec:iron_calib}. 

After the data is adjusted, the heading can be calculated as the arctangent between the y and x component: this is because while the the heading can be at any angle, (arc)sine and (arc)cosine can only determine if this angle is in the first or fourth quadrant, and in the first and second quadrant, respectively; \texttt{atan2(y, x)} considers instead the signs of x and y and can determine any angle. 

The process is showed in listing \ref{lst:magcal}.

\begin{lstlisting}[language=PythonPlus, label={lst:magcal}, caption={The magnetic field is read from the sensor, the calibration parameters are applied and the heading is computed.}]
def get_position():
	mx, my, mz = icm.magnetic

	corrected_xyz = np.dot(si, np.array([mx - hi[0], my - hi[1], mz - hi[2]]))
	
	heading_rad = atan2(corrected_xyz[1], corrected_xyz[0])
	
	if (heading_rad < 0):
		heading_rad += 2*np.pi
	
	if (heading_rad > 2*np.pi):
		heading_rad -= 2*np.pi
	
	heading = np.rad2deg(heading_rad)
	
\end{lstlisting}

\subsection{\texttt{accel.py}}
The accelerometer sensor uses the \texttt{i2c} communication protocol. Since the Raspberry has a physical bus that was already in use by the magnetometer, 
a software one was defined, as explained in \ref{sec:communication}.

In this case no library was used; the process to compute the tilt angle is roughly the same explained for the magnetometer, i.e. the arctan is considered between y and the hypotenuse between x and z. But there is also a slight more complicated setup process. 

To begin with, the bus is defined at the i2c port 11, and the device address is \texttt{0x68}; then the register \texttt{PWR\_MGMT\_1} is set. This register allows the user to configure the power mode and clock source \cite{sparkfun}.

\begin{lstlisting}[language=PythonPlus, caption=Sensor initialization.]
power_mgmt_1 = 0x6b
power_mgmt_2 = 0x6c

bus = smbus.SMBus(11)
address = 0x68
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

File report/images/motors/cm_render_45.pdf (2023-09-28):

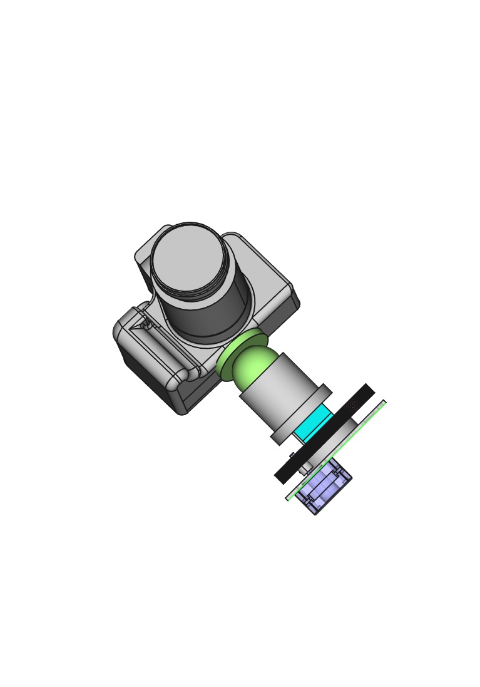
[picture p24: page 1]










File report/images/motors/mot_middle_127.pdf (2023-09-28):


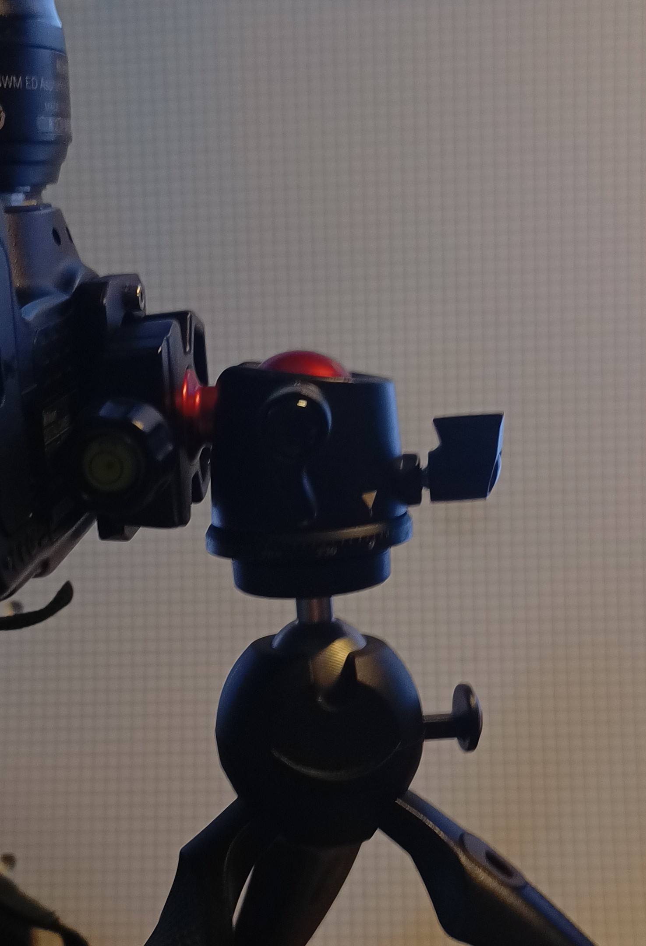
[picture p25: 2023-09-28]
report/images/motors/cm_photo3.jpg

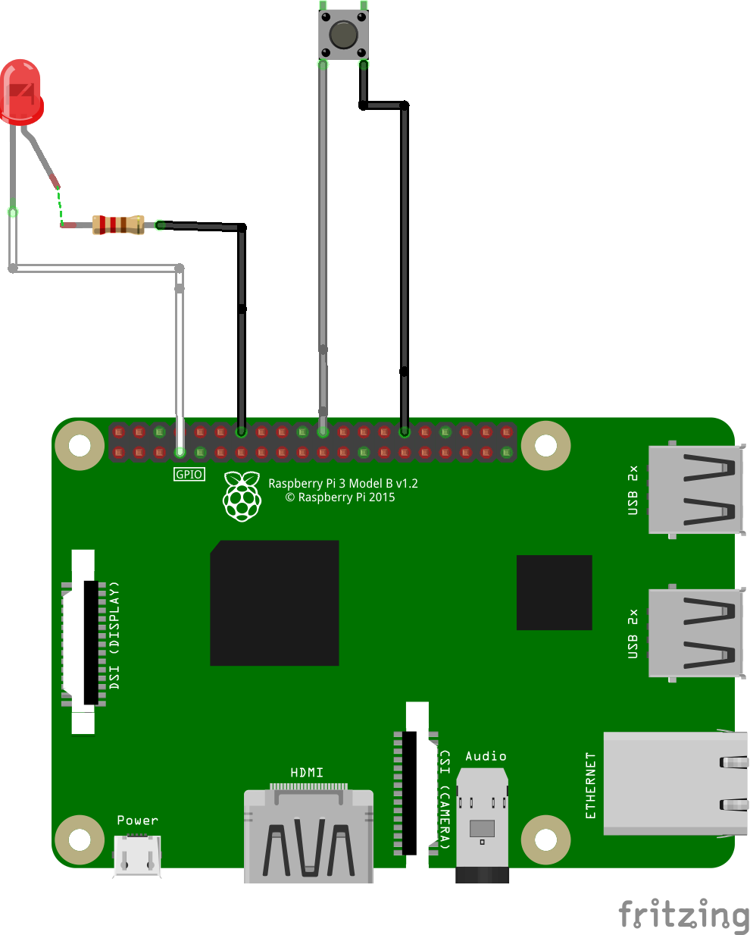
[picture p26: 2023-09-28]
report/images/electronic/input.png

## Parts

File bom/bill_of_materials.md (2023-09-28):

# Bill of materials

This file shows all the used components. 

### Electronics
Check the report for additional reference about the electronic components. 

|Name  |Number  |
| ---- | :----: |
| Raspberry Pi 3B+ | x1 |
| GY-521 MPU6050 | x1 |
| MT3608 | x2 |
| u-blox Neo 6M | x1 | 
| Adafruit ICM20948 | x1 |
| L298N | x1 |
| L9110 | x2 | 
| 2V led | x1 |
| $260 \Omega$ resistor | x1 |
| on-off button | x1 |
| unipolar switch | x1 |
| TP4056 | x1 |
| Lipo 2200 mAh battery | x1 |
| Nema 17HS15 | x1 |
| Nema 174023 | x2 |

### Other/Not counted

| Name | Size/Description | Number |
| ---- | --- | :----: |
| Ball bearing | 16x31x10mm | x4 |
| Ball bearing | 10x30x9mm| x1 |
| Axial ball bearing | 65x90x18mm | x1 |
| Screws | Used to fix the ball bearing holder in <br/>the _middle_ part | x8 |
| Bolts and Nuts | Assortment of M2, M3, M4 of various <br/>length - 4mm to 20mm | |
| M2.5 Nuts | Used to fix the Raspberry | x4 |
| Jump wires | Assortment of male-male, female-famale <br/> and male-female | |

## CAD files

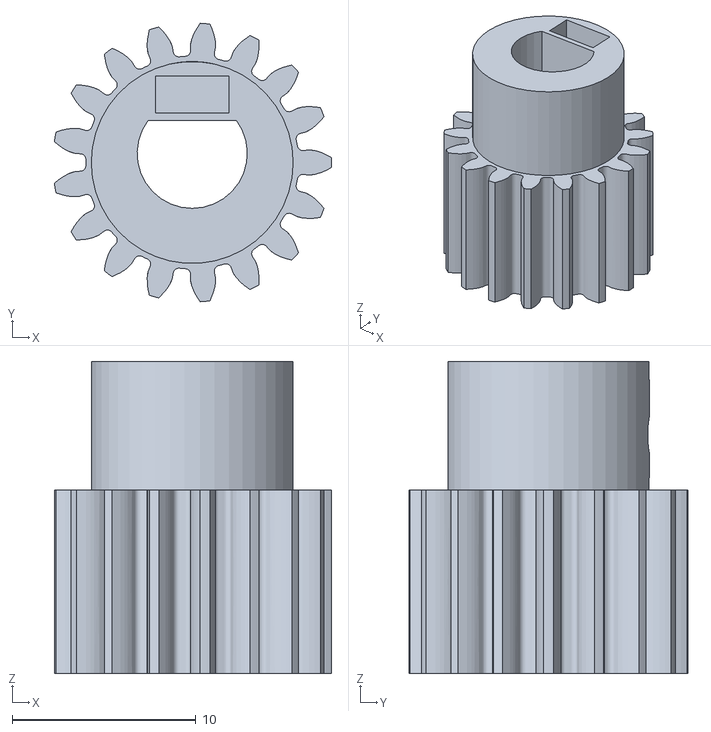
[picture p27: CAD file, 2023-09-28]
cad/stl/base/gears/gear_17.stl
15.1 x 15.2 x 17.0

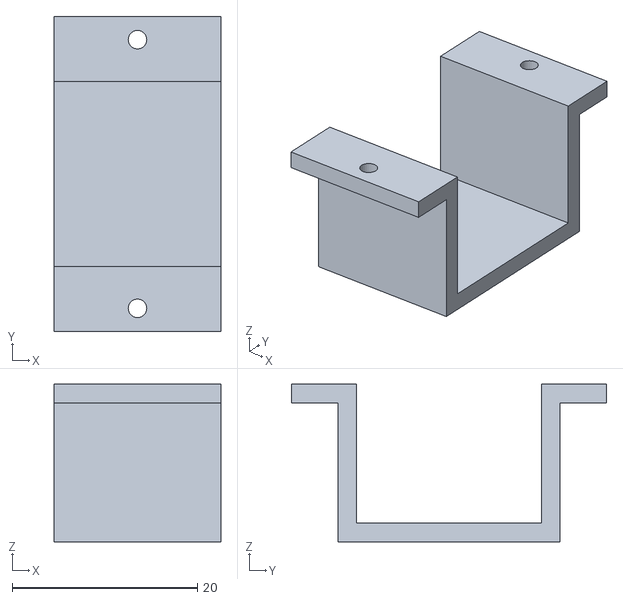
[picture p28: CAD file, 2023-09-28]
cad/stl/base/inner_components/MT3608_holder.stl
18.0 x 34.0 x 17.0

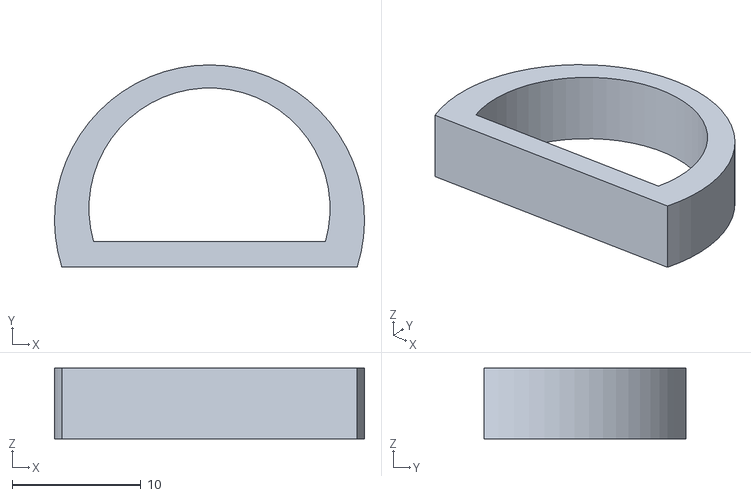
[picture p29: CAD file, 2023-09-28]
cad/stl/middle/auxilary_parts/cable_holder.stl
24.1 x 15.7 x 5.50

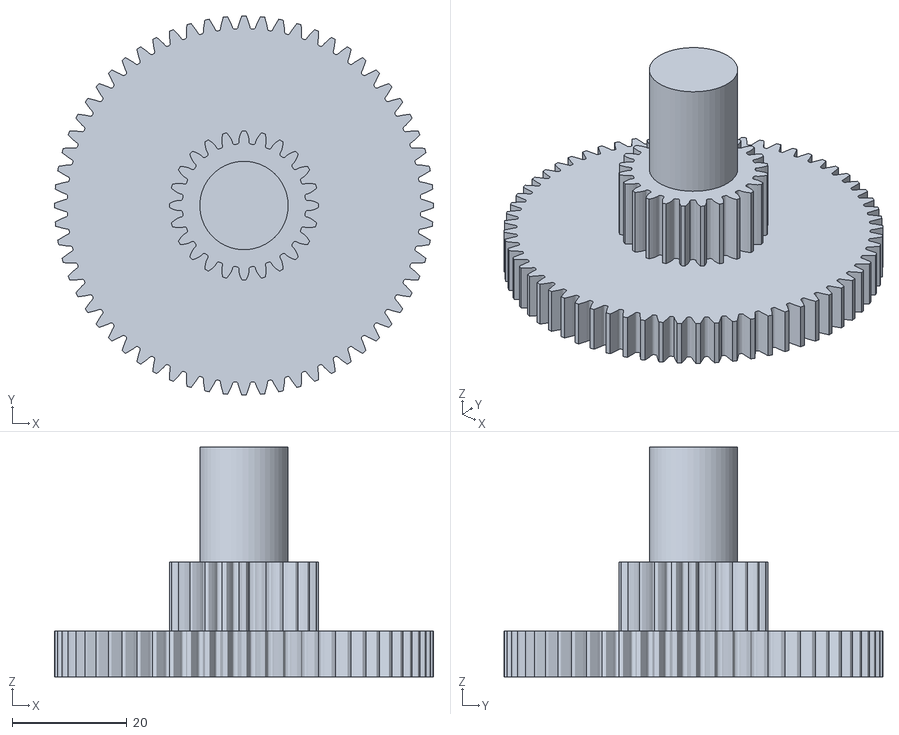
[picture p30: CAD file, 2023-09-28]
cad/stl/middle/gears/double_gear.stl
66.0 x 66.0 x 40.0

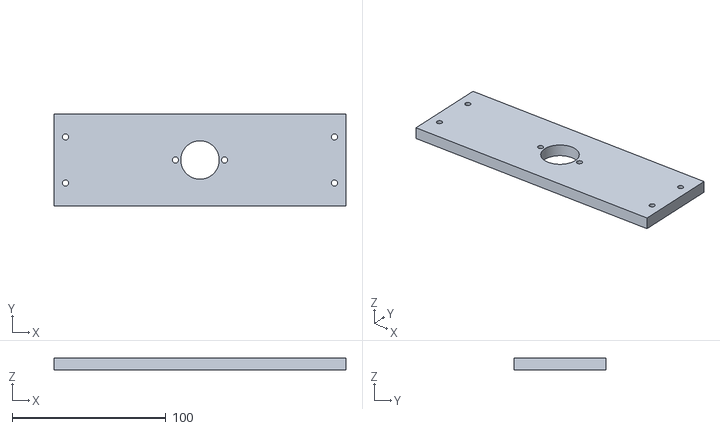
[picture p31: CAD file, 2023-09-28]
cad/stl/middle/main_components/middle_bottom.stl
190.0 x 60.0 x 8.00

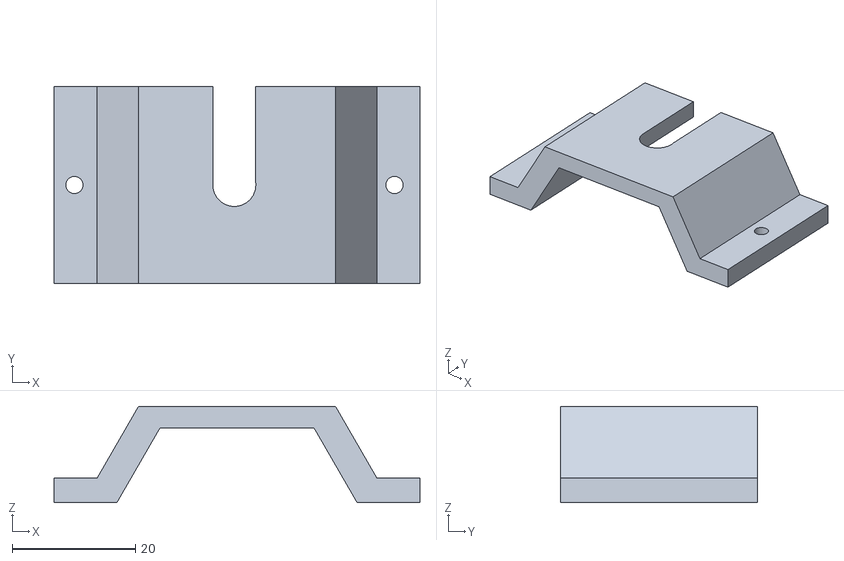
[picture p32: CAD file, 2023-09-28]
cad/stl/top/auxiliary_parts/camera_support.stl
59.5 x 32.0 x 15.7

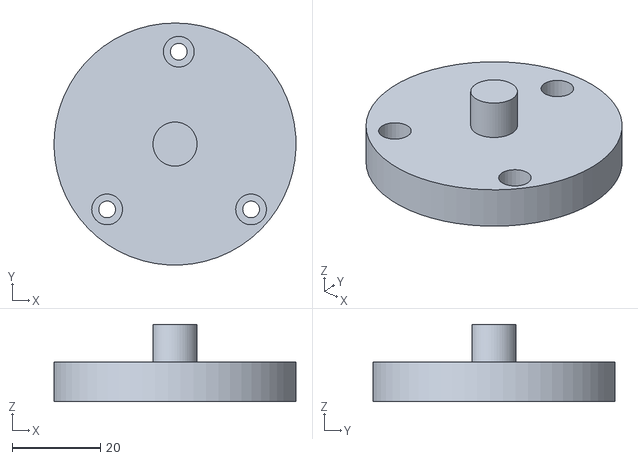
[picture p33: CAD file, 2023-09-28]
cad/stl/top/base/bearing_and_gear_126_holder.stl
54.9 x 54.9 x 17.5

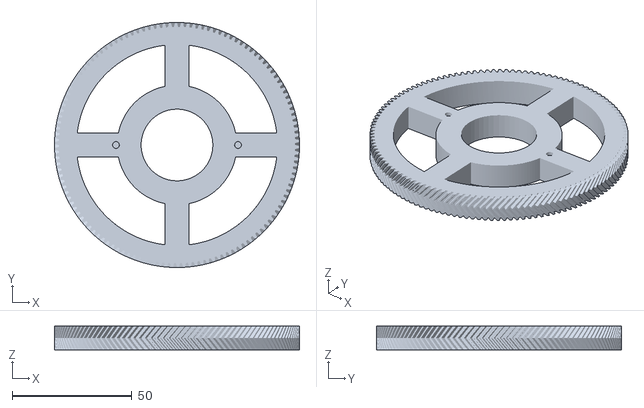
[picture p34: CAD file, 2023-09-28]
cad/stl/top/gears/helicoidal_gear_126.stl
102.4 x 102.4 x 10.0

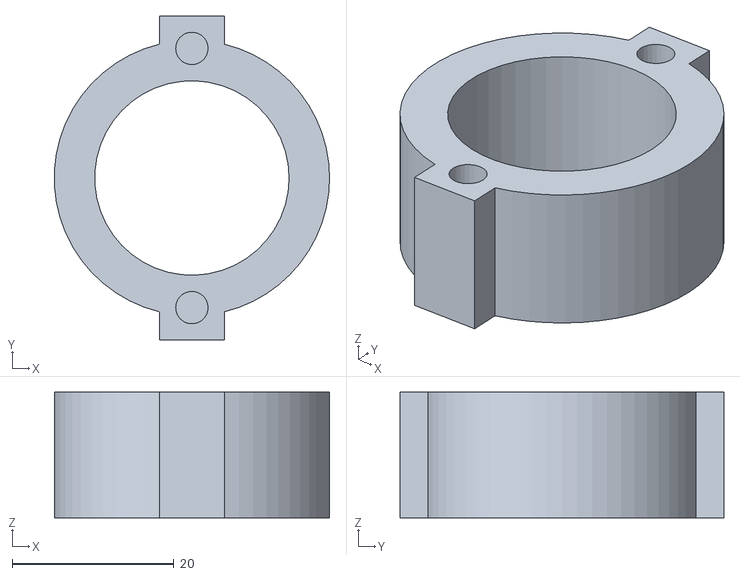
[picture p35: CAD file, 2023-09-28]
cad/stl/base/gears/gear_64_bottom.stl
34.0 x 40.0 x 15.5

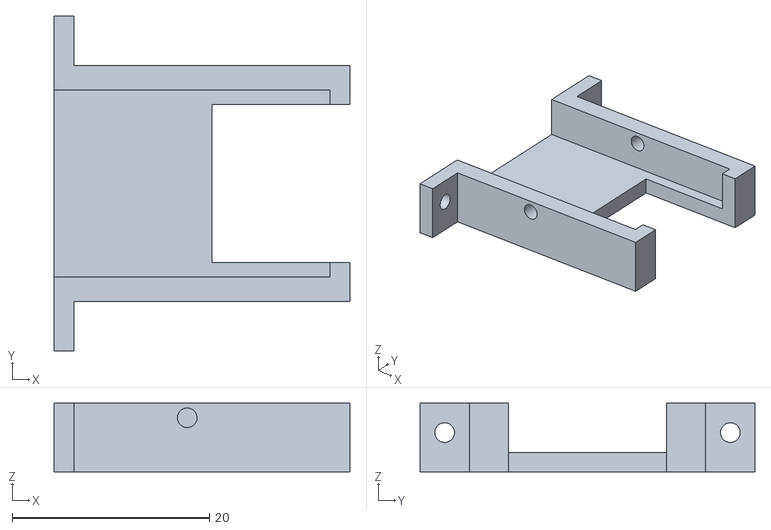
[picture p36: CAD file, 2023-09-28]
cad/stl/base/inner_components/TP4056_holder.stl
30.0 x 34.0 x 7.00

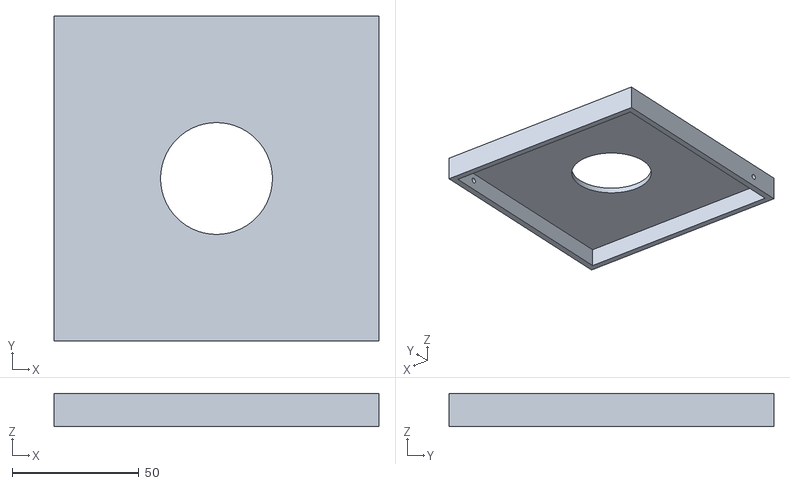
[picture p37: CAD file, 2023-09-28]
cad/stl/base/main_components/lid.stl
128.0 x 128.0 x 13.1

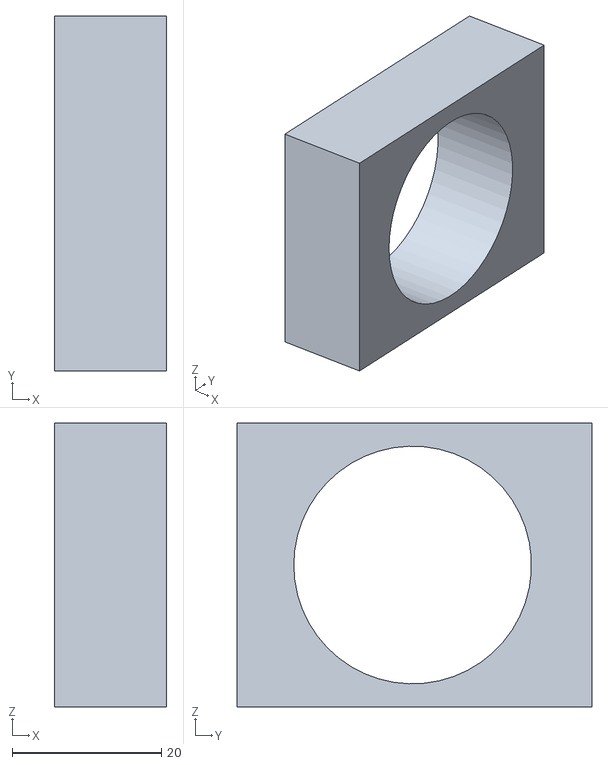
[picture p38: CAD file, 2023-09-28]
cad/stl/middle/auxilary_parts/bearing_holder.stl
15.0 x 47.5 x 38.0

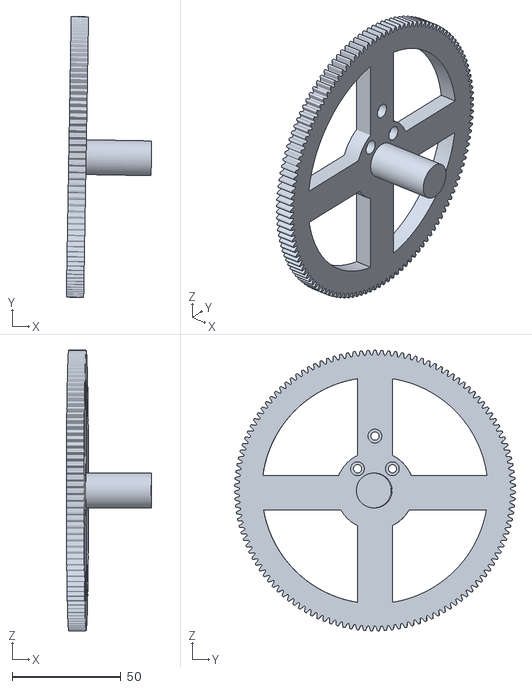
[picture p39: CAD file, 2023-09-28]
cad/stl/middle/gears/gear_127.stl
39.3 x 129.1 x 129.0

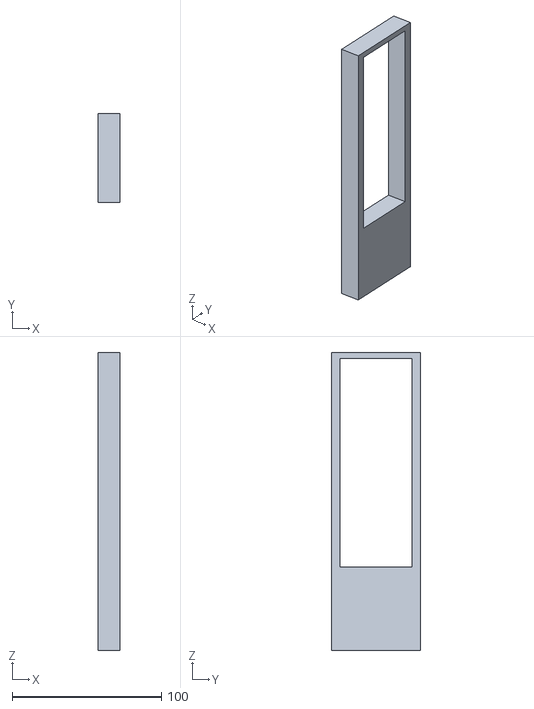
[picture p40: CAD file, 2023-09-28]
cad/stl/middle/main_components/middle_left.stl
15.0 x 60.0 x 200.0

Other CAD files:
cad/stl/top/auxiliary_parts/middle_gear_side_attach.stl
cad/stl/top/base/base.stl
cad/stl/top/gears/helicoidal_gear_17.stl
cad/stl/base/gears/gear_64_top.stl
cad/stl/base/main_components/UNC-1-4_screwed_hole.stl
cad/stl/base/main_components/base.stl
cad/stl/base/main_components/inner_plane.stl
cad/stl/middle/auxilary_parts/adafruit_holder.stl
cad/stl/middle/gears/gear_17.stl
cad/stl/middle/main_components/middle_right.stl
cad/stl/top/auxiliary_parts/bearing_side_attach.stl

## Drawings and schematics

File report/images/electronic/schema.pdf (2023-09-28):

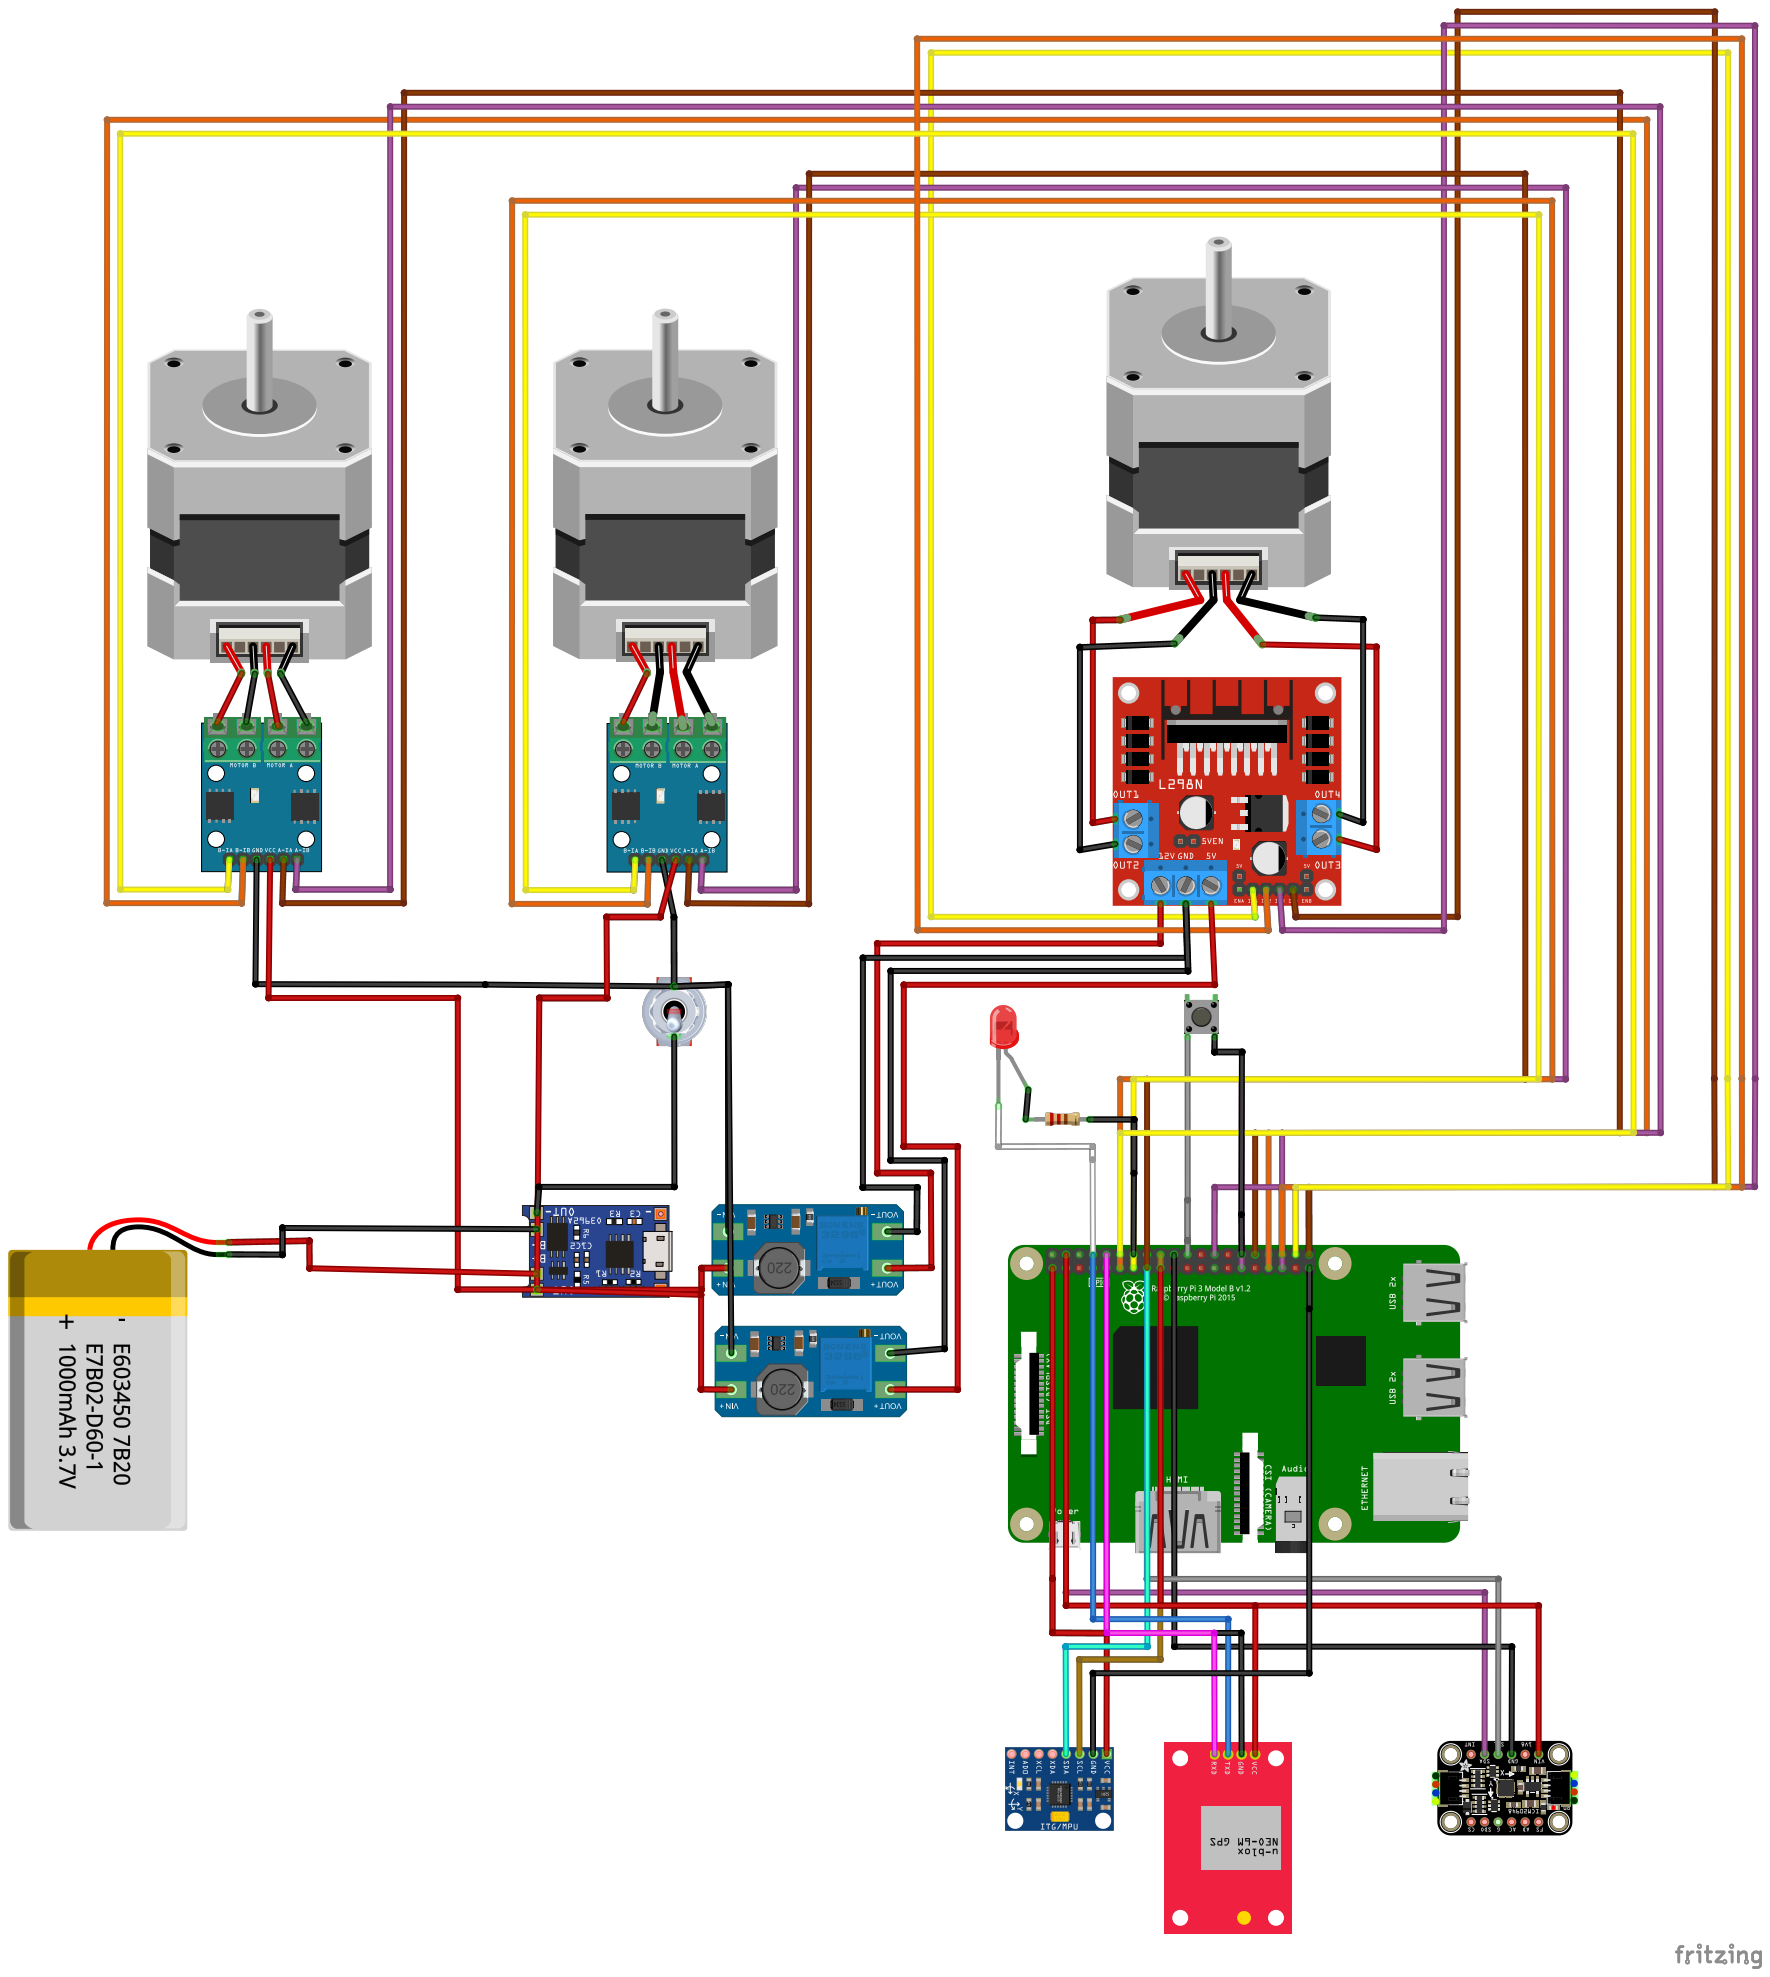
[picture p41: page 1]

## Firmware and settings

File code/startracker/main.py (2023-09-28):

import asyncio
import RPi.GPIO as GPIO 
from lib import gps, compass, motors, accel
from datetime import date
import time
import wmm2020
import numpy as np
import os
GPIO_BUTTON=25              # The GPIO pin the button is attached to
GPIO_LED=4                  # The GPIO pin the led is attached to
LONGPRESS_SHUTDOWN=10       # If button is held this length of time, shut down the system
LONGPRESS_START_STOP=3      # If button is held this length of time, start/stop the star tracker
""" 
    after the system gets in the right tilt position, we may want to move the camera, and this can make the system go in the wrong tilt position
    so we wait WAIT_BETWEEN_ADJUST_TILT seconds before adjusting again the system in the correct position
"""
WAIT_BETWEEN_ADJUST_TILT=15 
                            

is_running = False      # status of the star tracker (running/not running)
is_ready_1 = False      # wether the star tracker points to north and we have gps data
is_ready_2 = False      # wether the star tracker is ready to track (in the correct position)
gps_data = [None, None, None, None]         # gps position - lat, lon, alt, date
compass_data = None     # distance from north (degrees)

GPIO.setmode(GPIO.BCM) 
GPIO.setup(GPIO_BUTTON, GPIO.IN, pull_up_down=GPIO.PUD_UP) 
GPIO.setup(GPIO_LED,GPIO.OUT) 

async def listen_accel():
    print("Listen accel started")
    gear_ratio1 = 64/17
    gear_ratio2 = 127/24
    
    global is_ready_1
    global is_ready_2
    global gps_data

    is_ok = False
    while True:
        if is_ready_1 and is_running:
            tilt_array = []
            for i in range(30):
                _tilt = accel.get_tilt() #tilt is negative
                print("got tilt of", _tilt, end="\r")
                tilt_array.append((_tilt*-1))
            
            _tilt = np.median(tilt_array)
            print("accel: tilt is", _tilt)
            if _tilt == 0:
                #we took no data because everything is 0
                continue
            distance = gps_data[0] - _tilt
            if distance < 1.5 and distance > -1.5:
                #now the user is going to mount the camera
                motors.lock_motor("y")
                #so the camera won't fall 
                if is_ok:
                    is_ready_2 = True
                    motors.lock_motor("x")
                    print("Motor locked for accel")
                    break
                is_ok = True
            else:
                is_ok = False
            
                rot2  = distance*gear_ratio2
                step1 = abs(int((rot2*gear_ratio1)/1.8))
                print("accel: we are at tilt", _tilt, "and need to go to", gps_data[0])
                print("accel:", step1, "steps needed to position correctly - distance is", distance)
                if distance > 0:
                    print("accel: I need to move clockwise")
                    motors.move("x", step1, clockwise=True)
                else:
                    print("accel: I need to move anticlockwise")
                    motors.move("x", step1, clockwise=False)
            await asyncio.sleep(WAIT_BETWEEN_ADJUST_TILT)
        await asyncio.sleep(1)    

async def tracking():
    while True:
        if is_ready_2 and is_running:
            print("tracking 10 seconds")
            #the led will flash for a few seconds, so the user has the time to press the shutter button on the camera before the tracking starts
            await asyncio.sleep(10)
            await motors.move_microstep("y", 1000, sleep=True) #1000 is a random number - is just a large number of steps
        else:
            await asyncio.sleep(1)

def listen_gps():
    print("Listen gps task started")
    # while True:
    _gps_data = gps.get_gps_data()
    print("Got gps data:", _gps_data)
    if _gps_data != None and _gps_data[0] != 0:
        global gps_data
        global compass_data
        global is_ready_1
        gps_data[0] = _gps_data[0]
        gps_data[1] = _gps_data[1]
        gps_data[2] = _gps_data[2]
        gps_data[3] = _gps_data[3]
        if compass_data != None:
            is_ready_1 = True
        else:
            print("gps ready, but not compass, can't set is_ready_1 to true")
        # break
        return True
    # else:
    #     await asyncio.sleep(1)
    return False
        

async def control_led():
    print("Control led started")
    #shut the led off
    GPIO.output(GPIO_LED,GPIO.LOW) 

    while True:
        print("is_read_1", is_ready_1)
        print("is_ready_2", is_ready_2)
        if is_ready_1 and not is_ready_2:
            #light the led
            GPIO.output(GPIO_LED,GPIO.HIGH) 
        elif is_ready_2:
            GPIO.output(GPIO_LED,GPIO.LOW) 
            print("LED: we are ready and tracking, countdown...")
            pos = 0
            for i in [1, 1, 2, 3, 5, 8, 13, 21, 34, 55, 89, 144]: #fib sequence
                #this gives us about 9 seconds of blinking
                time2sleep = 1/i
                print("blink time2sleep:", time2sleep)
                pos += 1
                for j in range(pos):
                    #do pos blinks for time time
                    GPIO.output(GPIO_LED,GPIO.HIGH) 
                    print("BLINK")
                    time.sleep(time2sleep)
                    GPIO.output(GPIO_LED,GPIO.LOW) 
                    print("NOT BLINK")
                    time.sleep(time2sleep)
                    
            counter_seconds = 0
            while is_ready_2:
                print("now we have to blink fast every 30 seconds")
                print((30 - counter_seconds), "seconds to blink")
                if counter_seconds == 0:
                    print("Counter seconds:", counter_seconds)
                    #blink
                    for l in range(2):
                        GPIO.output(GPIO_LED,GPIO.HIGH) 
                        time.sleep(0.05)
                        GPIO.output(GPIO_LED,GPIO.LOW) 
                        time.sleep(0.05)

                counter_seconds += 1
                counter_seconds = counter_seconds%30
                await asyncio.sleep(1)
        await asyncio.sleep(1)

def listen_compass():
    print("listen compass started")
    # while True:
    compass_array = []
    compass_array_shifted = []
    for i in range(30):
        _compass = compass.get_position()
        if _compass > 180:
            compass_array_shifted.append(360 - _compass)
        else:
            compass_array_shifted.append(_compass)
        compass_array.append(_compass)
    
    _compass_shifted = np.median(compass_array_shifted)
    _compass = np.median(compass_array)

    print("read compass:", _compass, "and shifted:", _compass_shifted)
    
    # if gps_data == None or gps_data[0] == None or gps_data[2] == None or gps_data[3] == None:
    #     print("compass: gps data is still None, continue")
    #     # await asyncio.sleep(1)
    #     # continue
    #     return False
    
    current_date = gps_data[3]
    year = current_date.year
    elapsed = current_date.toordinal() - date(year, 1, 1).toordinal()
    yeardec = year + (elapsed/365)
    
    mag = wmm2020.wmm(gps_data[0], gps_data[1], gps_data[2]/1000, yeardec)        
    decl = mag.decl.data[0,0]
    print("Declination is", decl)
    _compass += decl
    _compass = _compass%360
#        global gps_data
    global compass_data
    global is_ready_1

    if _compass_shifted < 5:
    # if _compass_shifted > 175:
        #we are within 2 degrees from north, let's block the motor and signal to the user with 5 vibrations:
        for i in range(5):
            print("we found the north, vibrate three times for one second")
            motors.vibrate("z", 0.2)
            time.sleep(0.3)
        compass_data = _compass_shifted
        motors.lock_motor("z")
        print("\nMotor locked for compass")
        if gps_data[0] != None:
            is_ready_1 = True
        else:
            print("compass ready, but not gps_data, can't set is_ready_1 to true")
        # break
        return True


    if  _compass < 180: #we are, e.g., at 40° from north and must turn anticlockwise
        print("we should turn a bit anticlockwise, vibrate once for", _compass/90, "seconds")
        # let's signal it to the user with a vibrations:
        motors.vibrate("z", _compass/90) #vibration in seconds: 180 = 2 sec, 90 = 1 sec etc.
        # motors.vibrate("z", (180 - _compass)/90) #vibration in seconds: 180 = 2 sec, 90 = 1 sec etc.
        time.sleep(3) #time for the user to make the adjustement
    else: #we are, e.g. 330° = 30° from north and must turn clockwise
        print("we should turn a bit clockwise, vibrate twice for", _compass/180, "seconds each")
        # let's signal it to the user with two vibrations:
        motors.vibrate("z", (360 - _compass)/180) #it's like (_compass/90)/2
        # motors.vibrate("z", (_compass - 180)/180) #it's like (_compass/90)/2
        time.sleep(0.5)
        motors.vibrate("z", (360 - _compass)/180) #it's like (_compass/90)/2

        time.sleep(3) #time for the user to make the adjustement

    
    # await asyncio.sleep(1)
    return False

async def listen_button():
    while True:
        await asyncio.sleep(1)

        if GPIO.input(GPIO_BUTTON) == False: # Listen for the press 
            print("button: someone pressed")
            pressed_time=time.time()
            while GPIO.input(GPIO_BUTTON) == False: 
                time.sleep(0.1)

                elapsed_time=time.time()-pressed_time
                print("pressing time:", elapsed_time, end="\r")
                if GPIO.input(GPIO_BUTTON): #the pressing stopped
                    if elapsed_time > LONGPRESS_START_STOP and elapsed_time < LONGPRESS_SHUTDOWN:
                        global is_ready_1
                        global is_ready_2
                        global is_running
                        
                        if not is_ready_1:
                            print("Cannot start tracking, ready_1 is false")
                            break
                        if is_ready_1 and not is_running: #pressing the button before we have gps data and pointing to north does nothing
                            is_running = True
                            break
                        else:    
                            print("Stopping tracking")
                            is_running = False
                            is_ready_2 = False
                    elif elapsed_time > LONGPRESS_SHUTDOWN:
                        print("SHUTTING SYSTEM DOWN")
                        os.system("sudo shutdown now")
        else:
            print("button: no pressing detected")
                
async def listen_gps_compass():
    while not listen_gps():
        asyncio.sleep(1)
    while not listen_compass():
        asyncio.sleep(1)
    

async def main():
    task_button = asyncio.create_task(listen_button()) 
    task_gps_compass = asyncio.create_task(listen_gps_compass())
    task_tracking = asyncio.create_task(tracking())
    task_accel = asyncio.create_task(listen_accel())
    task_led = asyncio.create_task(control_led())
    await asyncio.gather(task_button, task_gps_compass, task_tracking, task_accel, task_led) 

if __name__ == "__main__":
    asyncio.run(main())
